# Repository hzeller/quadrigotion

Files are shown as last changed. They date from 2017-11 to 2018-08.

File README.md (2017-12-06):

Quadrigotion: Multiple Motor Drivers, one connector
============================================================

Often it is useful to have all the motor drivers needed for a machine
on a separate circuit board to be able to mount it to a heatsink or close
to the action. This is what this project is about.
The name **Quadrigotion** is a word amalgamated from 'Quadriga' (Four
horses powering a chariot) and 'Motion'.

Motivation for this project to have motor drivers easily replacable and
testable on my various 3D printers and CNC machines. Since I am also
[developing motion control software][BeagleG], I might have an unusual
high demand for this :)

The idea is to have a common connector type, described below, and various
implementations of that concept. The first implementation is using a TMC2660,
which is the 'big brother' of the more well-known TMC2100.

Other implementations are conceivable e.g. with Pololu modules, DRV8825, or
super high current and voltage drivers for heavy CNC machines.
Implementations can be super bare-bone and not use the SPI connection or
could be configured via SPI using a shift-register and digital potentiometers
if the chips can't be configured with SPI directly.
While the first Quadrigotion implementation happens to also have four motor
drivers, this could of course extend in the future.

The Connector
--------------

The digital input is provided with an IDC connector with 16 pins (2x8) or
20 pins (2x10).
It features a SPI bus to send configuration data and also read motor/driver
status (the actual protocol is of implementation-dependent, but they all can
share the same hardware interface).

| Desc | Pin | Pin | Desc
|---:|:---:|:---:|:---
| GND  | 1 | 2 | VCC (3.3V-5V)
| All Motors ~Enable | 3 | 4 | (not connected; reserved for fault-out)
| ~CS (SPI) | 5 | 6 | CLK (SPI)
| MISO (SPI) | 7 | 8 | MOSI (SPI)
| Step #1 | 9 |  10 | Dir #1
| Step #2 |  11 |  12 | Dir #2
| Step #3 |  13 |  14 | Dir #3
| Step #4 |  15 |  16 | Dir #4 -------- END IDC 16 variant
| Step #5 |  17 |  18 | Dir #5
| Step #6 |  19 |  20 | Dir #6 -------- END IDC 20 variant

It is easy to see that extending the driver count would just require a wider
IDC connector; the serial configuration interface can deal with any
number. A 16 pin IDC connector allows for 4 steppers, the next configuration
with 20 pins would allow for six drivers.

A single Enable-pin is provided that affects all drivers. This makes it easy
to wire up that signal directly e.g. for emergency buttons.
If more individual control of each driver is needed, this can be done via
the SPI connection.

The fast signals for each stepper, step and dir, are provided in
a parallel input with two lines per stepper.

A Quadrigotion connector has a single ChipSelect signal; multiple drivers
on each implementation have to share that bus, e.g. by internally being
organized as a shift register that latches when ~CS goes high again.

One pin (pin 4) is not connected yet, but it is reserved for fault detection
output (e.g stalling, overheating or over-current).

In an upcoming project, I'll build a breakout board to work with [BeagleG].

TMC2660 Implementation
----------------------

The first implementation is based on the TMC2660, a feature-rich motor driver
that can drive up to 4A (2.8A RMS). The 40mmx125mm PCB is a four layer board
which duals as heat conductor for cooling. Multiple M2.5 mounting holes allow
to firmly mount it to a heatsink and get even pressure to individual silicone
heatsink pads.
Power is provided via a 4-pin JST VH connector (3.96mm pitch),
circuit protected with an automotive ATC Mini 297 blade fuse.

You find the gerbers in the [fab/](./fab) directory. Board is also
[shared on OshPark]. Cave: since this is the very first version, no
testing has been done yet with a physical board.

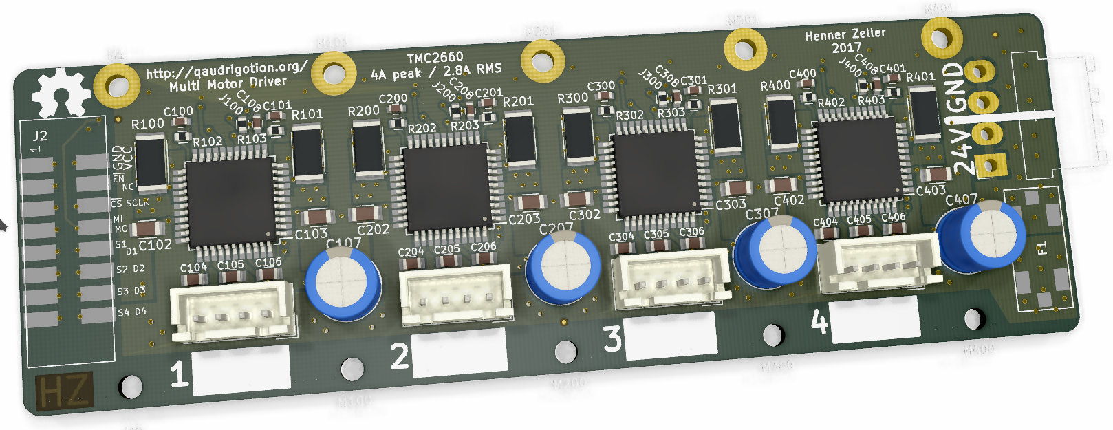
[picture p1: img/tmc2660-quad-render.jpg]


[BeagleG]: https://github.com/hzeller/beagleg
[shared on OshPark]: https://oshpark.com/shared_projects/M0SQCRdL

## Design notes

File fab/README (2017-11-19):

This directory contains gerber output files ready for fabbing.
These are generated from the KiCad boards.

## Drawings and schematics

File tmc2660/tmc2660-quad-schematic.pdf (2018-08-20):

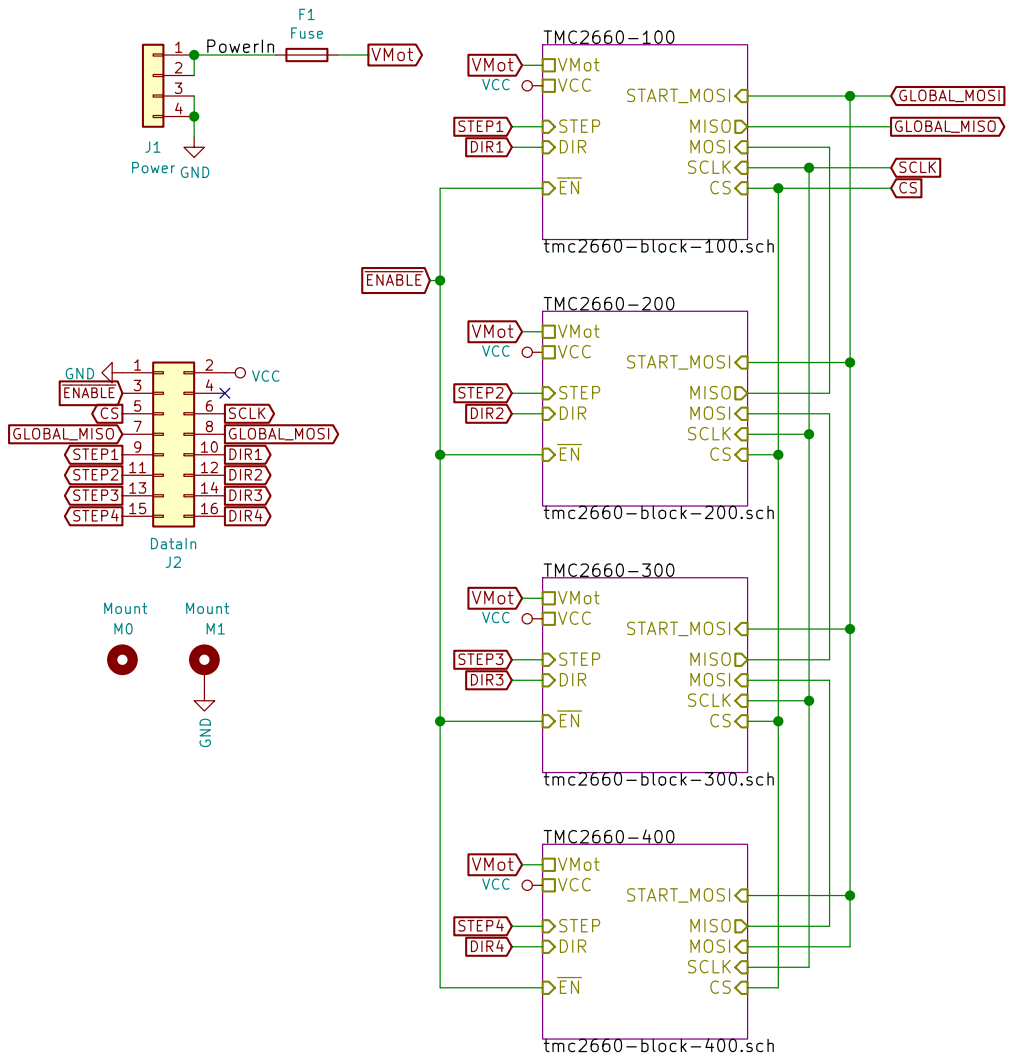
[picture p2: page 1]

File: tmc2660-quad.sch Sheet: / http://quadrigotion.org/

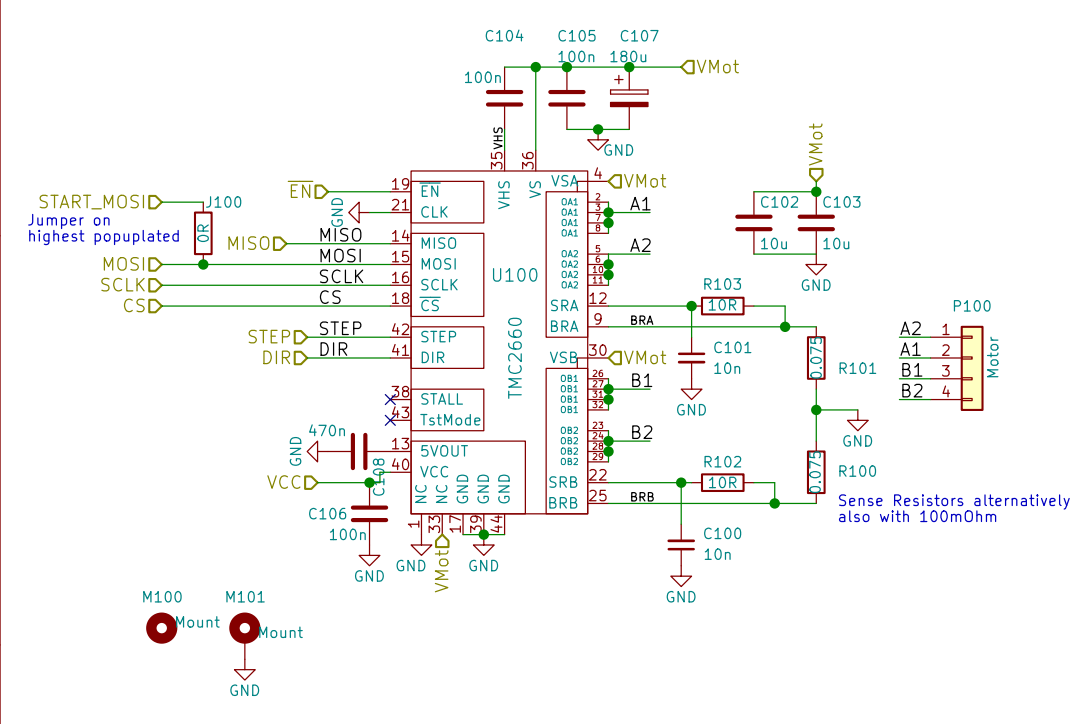
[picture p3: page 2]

Sense Resistors alternatively also with 100mOhm

File: tmc2660-block-100.sch Sheet: /TMC2660-100/ http://quadrigotion.org/

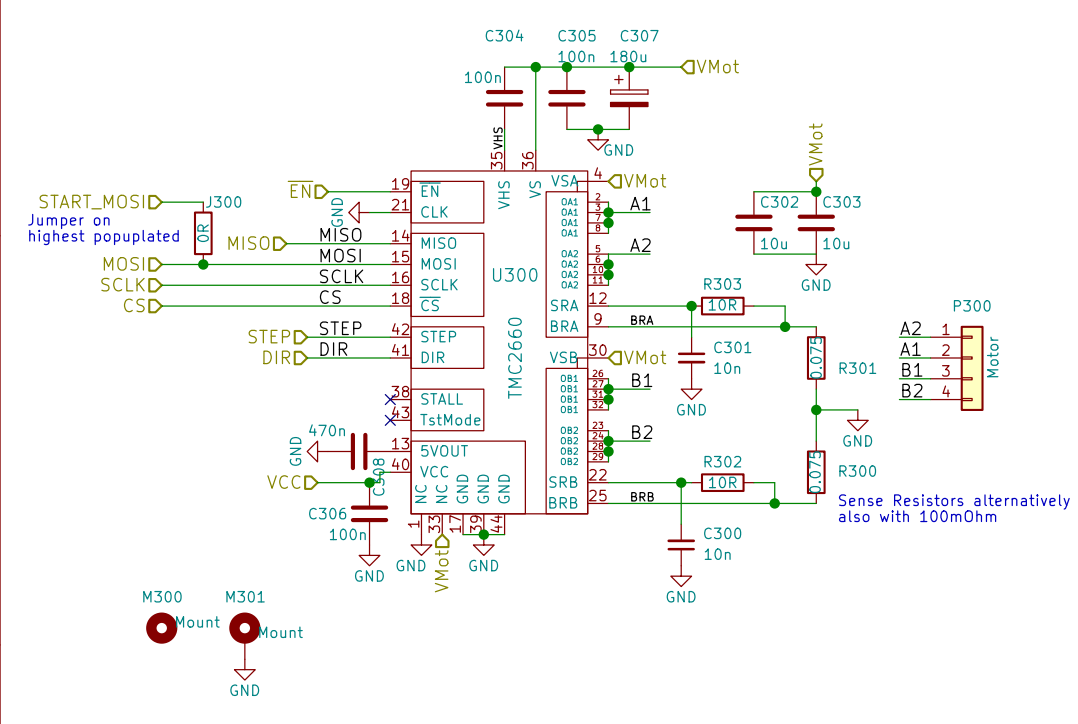
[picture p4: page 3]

Sense Resistors alternatively also with 100mOhm

File: tmc2660-block-300.sch Sheet: /TMC2660-300/ http://quadrigotion.org/

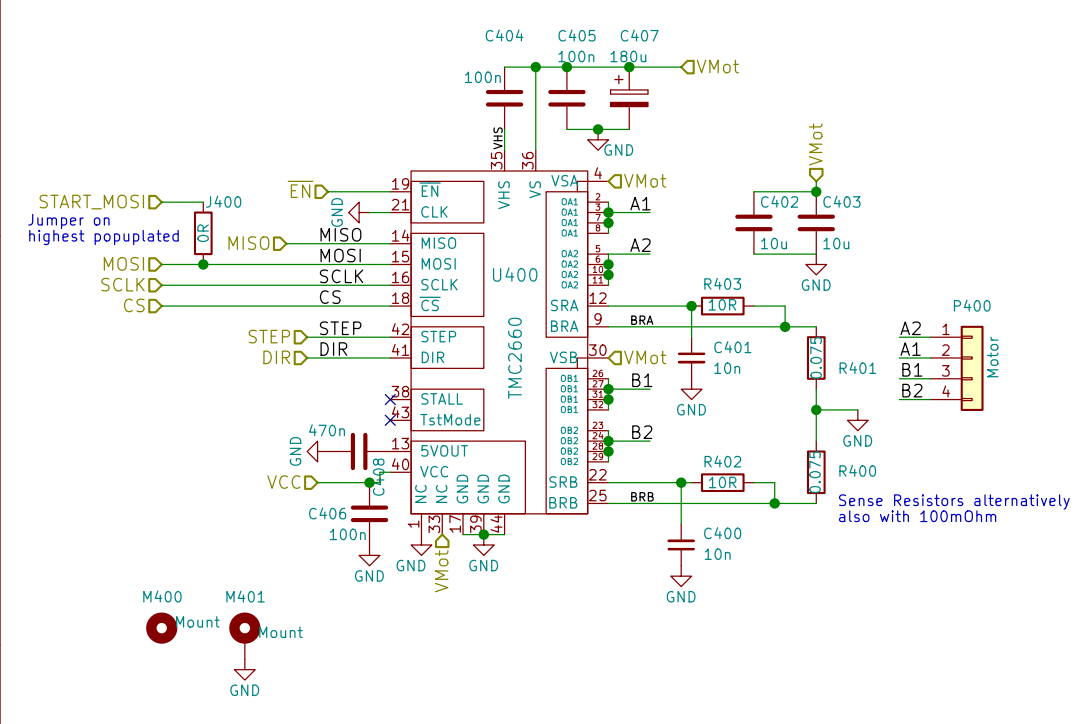
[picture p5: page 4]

Sense Resistors alternatively also with 100mOhm

File: tmc2660-block-400.sch Sheet: /TMC2660-400/ http://quadrigotion.org/

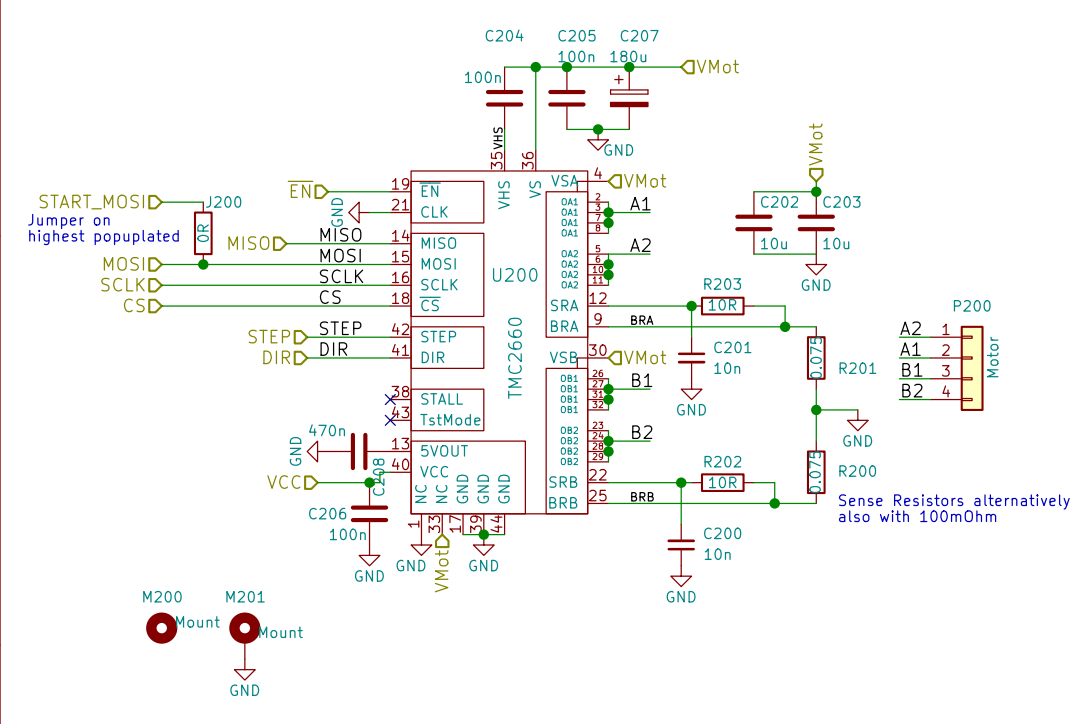
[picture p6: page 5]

Sense Resistors alternatively also with 100mOhm

File: tmc2660-block-200.sch Sheet: /TMC2660-200/ http://quadrigotion.org/

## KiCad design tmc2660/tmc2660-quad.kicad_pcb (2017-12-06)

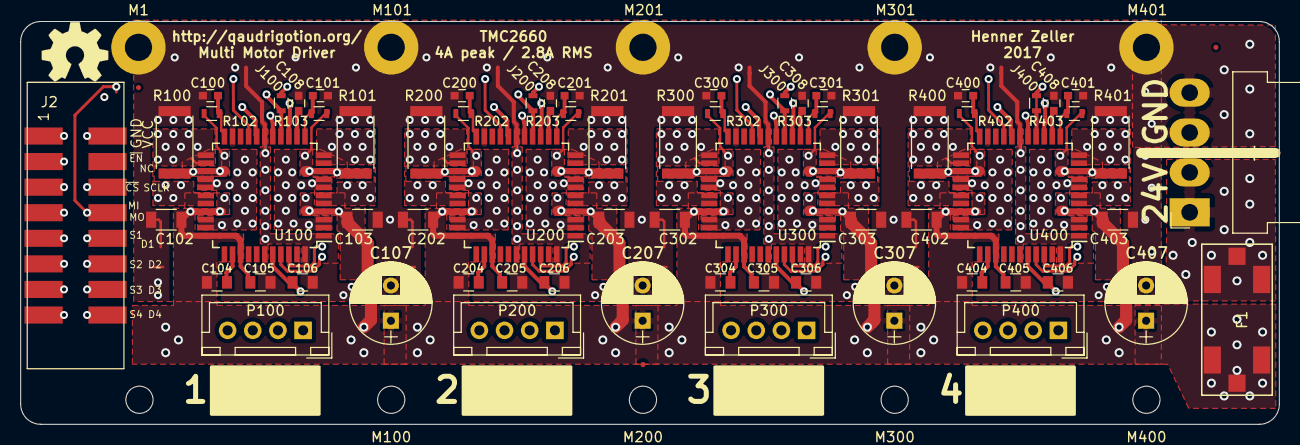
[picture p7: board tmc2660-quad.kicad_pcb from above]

Board: 4 copper layers, 125.0 x 40.0 mm, 77 parts (0 on the bottom side), 60 nets.

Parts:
C100, C101, C200, C201, C300, C301, C400, C401: 10n; C_0603
C102, C103, C202, C203, C302, C303, C402, C403: 10u; C_1206
C104, C105, C106, C204, C205, C206, C304, C305, C306, C404, C405, C406: 100n; C_0805
C107, C207, C307, C407: 180u; CP_Radial_D8.0mm_P3.50mm
C108, C208, C308, C408: 470n; C_0603
F1: Fuse; BladeFuse-Mini_Keystone-3586
J1: Power; JST_VH_B4PS-VH_2x4x3.96mm_Horizontal
J2: DataIn; IDC_Header_SMD_16pins
J100, J200, J300, J400: 0R; R_0603
M0, M100, M200, M300, M400: Mount; MountingHole_2.7mm_M2.5
M1, M101, M201, M301, M401: Mount; MountingHole_2.7mm_M2.5_Pad
P100, P200, P300, P400: Motor; JST_XH_B04B-XH-A_04x2.50mm_Straight
R100, R101, R200, R201, R300, R301, R400, R401: 0.075; R_2512
R102, R103, R202, R203, R302, R303, R402, R403: 10R; R_0603
U100, U200, U300, U400: TMC2660; LQFP-44_10x10mm_Pitch0.8mm

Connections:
/PowerIn: F1.2, J1.1, J1.2
/TMC2660-100/A1: P100.2, U100.2, U100.3, U100.7, U100.8
/TMC2660-100/A2: P100.1, U100.5, U100.6, U100.10, U100.11
/TMC2660-100/B1: P100.3, U100.26, U100.27, U100.31, U100.32
/TMC2660-100/B2: P100.4, U100.23, U100.24, U100.28, U100.29
/TMC2660-100/BRA: R101.1, R103.2, U100.9
/TMC2660-100/BRB: R100.1, R102.1, U100.25
/TMC2660-100/VHS: C104.2, U100.35
/TMC2660-200/A1: P200.2, U200.2, U200.3, U200.7, U200.8
/TMC2660-200/A2: P200.1, U200.5, U200.6, U200.10, U200.11
/TMC2660-200/B1: P200.3, U200.26, U200.27, U200.31, U200.32
/TMC2660-200/B2: P200.4, U200.23, U200.24, U200.28, U200.29
/TMC2660-200/BRA: R201.1, R203.2, U200.9
/TMC2660-200/BRB: R200.1, R202.1, U200.25
/TMC2660-200/MISO: J100.2, U100.15, U200.14
/TMC2660-200/VHS: C204.2, U200.35
/TMC2660-300/A1: P300.2, U300.2, U300.3, U300.7, U300.8
/TMC2660-300/A2: P300.1, U300.5, U300.6, U300.10, U300.11
/TMC2660-300/B1: P300.3, U300.26, U300.27, U300.31, U300.32
/TMC2660-300/B2: P300.4, U300.23, U300.24, U300.28, U300.29
/TMC2660-300/BRA: R301.1, R303.2, U300.9
/TMC2660-300/BRB: R300.1, R302.1, U300.25
/TMC2660-300/MISO: J200.2, U200.15, U300.14
/TMC2660-300/VHS: C304.2, U300.35
/TMC2660-400/A1: P400.2, U400.2, U400.3, U400.7, U400.8
/TMC2660-400/A2: P400.1, U400.5, U400.6, U400.10, U400.11
/TMC2660-400/B1: P400.3, U400.26, U400.27, U400.31, U400.32
/TMC2660-400/B2: P400.4, U400.23, U400.24, U400.28, U400.29
/TMC2660-400/BRA: R401.1, R403.2, U400.9
/TMC2660-400/BRB: R400.1, R402.1, U400.25
/TMC2660-400/MISO: J300.2, U300.15, U400.14
/TMC2660-400/VHS: C404.2, U400.35
CS: J2.5, U100.18, U200.18, U300.18, U400.18
DIR1: J2.10, U100.41
DIR2: J2.12, U200.41
DIR3: J2.14, U300.41
DIR4: J2.16, U400.41
GLOBAL_MISO: J2.7, U100.14
GLOBAL_MOSI: J2.8, J100.1, J200.1, J300.1, J400.1, J400.2, U400.15
GND: C100.1, C101.2, C102.2, C103.2, C105.2, C106.2, C107.2, C108.2, C200.1, C201.2, C202.2, C203.2, C205.2, C206.2, C207.2, C208.2, C300.1, C301.2, C302.2, C303.2, C305.2, C306.2, C307.2, C308.2, C400.1, C401.2, C402.2, C403.2, C405.2, C406.2, C407.2, C408.2, J1.3, J1.4, J2.1, M1.1, M101.1, M201.1, M301.1, M401.1, R100.2, R101.2, R200.2, R201.2, R300.2, R301.2, R400.2, R401.2, U100.1, U100.17, U100.21, U100.39, U100.44, U200.1, U200.17, U200.21, U200.39, U200.44, U300.1, U300.17, U300.21, U300.39, U300.44, U400.1, U400.17, U400.21, U400.39, U400.44
unnamed: C100.2, R102.2, U100.22
unnamed: C101.1, R103.1, U100.12
unnamed: C108.1, U100.13
unnamed: C200.2, R202.2, U200.22
unnamed: C201.1, R203.1, U200.12
unnamed: C208.1, U200.13
unnamed: C300.2, R302.2, U300.22
unnamed: C301.1, R303.1, U300.12
unnamed: C308.1, U300.13
unnamed: C400.2, R402.2, U400.22
unnamed: C401.1, R403.1, U400.12
unnamed: C408.1, U400.13
SCLK: J2.6, U100.16, U200.16, U300.16, U400.16
STEP1: J2.9, U100.42
STEP2: J2.11, U200.42
STEP3: J2.13, U300.42
STEP4: J2.15, U400.42
VCC: C106.1, C206.1, C306.1, C406.1, J2.2, U100.40, U200.40, U300.40, U400.40
VMot: C102.1, C103.1, C104.1, C105.1, C107.1, C202.1, C203.1, C204.1, C205.1, C207.1, C302.1, C303.1, C304.1, C305.1, C307.1, C402.1, C403.1, C404.1, C405.1, C407.1, F1.1, U100.4, U100.30, U100.33, U100.36, U200.4, U200.30, U200.33, U200.36, U300.4, U300.30, U300.33, U300.36, U400.4, U400.30, U400.33, U400.36
~ENABLE: J2.3, U100.19, U200.19, U300.19, U400.19

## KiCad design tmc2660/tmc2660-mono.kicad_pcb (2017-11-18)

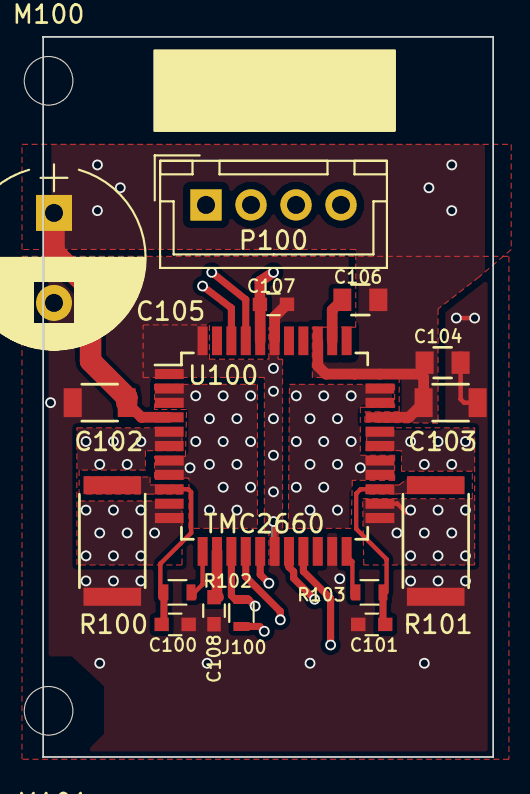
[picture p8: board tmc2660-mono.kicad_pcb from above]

Board: 4 copper layers, 25.0 x 40.0 mm, 18 parts (0 on the bottom side), 14 nets.

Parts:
C100, C101: 10n; C_0603
C102, C103: 10u; C_1206
C104, C106: 100n; C_0805
C105: 100u; CP_Radial_D10.0mm_P5.00mm
C107: 100n; C_0603
C108: 470n; C_0603
J100: 0R; R_0603
M100, M101: Mount; MountingHole_2.7mm_M2.5
P100: Motor; JST_XH_B04B-XH-A_04x2.50mm_Straight
R100, R101: 0.075; R_2512
R102, R103: 10R; R_0603
U100: TMC2660; LQFP-44_10x10mm_Pitch0.8mm

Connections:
/TMC2660-Block/A1: P100.2, U100.2, U100.3, U100.7, U100.8
/TMC2660-Block/A2: P100.1, U100.5, U100.6, U100.10, U100.11
/TMC2660-Block/B1: P100.3, U100.26, U100.27, U100.31, U100.32
/TMC2660-Block/B2: P100.4, U100.23, U100.24, U100.28, U100.29
/TMC2660-Block/BRA: C100.2, R100.1, R102.2, U100.9
/TMC2660-Block/BRB: C101.1, R101.1, R103.1, U100.25
/TMC2660-Block/MISO: J100.2, U100.14
GND: C100.1, C101.2, C102.2, C103.2, C104.2, C105.2, C107.2, C108.2, R100.2, R101.2, U100.1, U100.17, U100.21, U100.39, U100.44
unnamed: C106.2, U100.35
unnamed: C108.1, U100.13
unnamed: R102.1, U100.12
unnamed: R103.2, U100.22
VCC: C107.1, U100.40
VMot: C102.1, C103.1, C104.1, C105.1, C106.1, U100.4, U100.30, U100.33, U100.36

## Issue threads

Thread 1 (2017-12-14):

Affordabilty of PCBs

Duckle29, 2017-12-14:
I'm looking at getting a few of these made for sure, for my current printer, and was pricing it out.

At the current dimensions, 125 * 40mm I'm looking at 36 USD on easy EDA for 5 boards. That's 7.29 USD/board

If the board was instead 100 * 50mm (same area) you could panelize two of those together with v-grooves between them, which means you could get 10 boards for 32 USD, which would be  3.2 USD/board

This is because as long as you are within a 100x100mm panel, you fall into their cheap "this is what we have a price war on" price, but when you go over 100mm, you just get a "sq mm" price.

Duckle29, 2017-12-14:
I'll take a stab at fitting the design in that area in the weekend for sure :) I feel like moving the connectors at the ends down should do the trick.

hzeller, 2017-12-14:
Yeah, unfortunately, I couldn't squeeze it in 100mm, I tried :) Unfortunately, 4-layer boards really only start to be affordable with a little more quantity.

I have a couple of earlier version boards (version from 2017-11-19), that is mostly the same as the last version with only one minor issue that doesn't matter. If you are living in the US, I can send you one with domestic shipping (with components, it looks like [this](https://plus.google.com/u/0/+HennerZeller/posts/ZPCogGqCQMK). I have not tested it yet, hopefully this weekend will be time). So if you want one, send me your address via email.

Duckle29, 2017-12-14:
I'm in Denmark, but no need :) I kinda want to do the jiggling and give it a shot :P

I see that post you linked brought up a question I also have. Exact protocol. The datasheet isn't super clear on it. I was interested in how you got data out of them. I suppose just shifting in the appropriate query command to the appropriate chip, then keeping clocking until the message shifted its way through all of the chips?

hzeller, 2017-12-14:
I need to test that again; last time I played with it was a while back.
I think what happens is, while you shift in configuration bits, the current status bits come out on the other side, followed whatever is spilled over from the shift register.

So it should be possible to shift in 4x configuration data that then end up in the right chips and 4x status data has come out on the other side by then.

Duckle29, 2017-12-14:
Interesting

hzeller, 2017-12-14:
I'll update the readme once I played with it.

Duckle29, 2017-12-14:
6.3 Bus Architecture in the datasheet is what I needed to read. They work just like switch registers when chained, meaning that if you want to read from all of them, you can send 4 read commands, then clock in 160 pulses to shift that back to the master.

Duckle29, 2017-12-14:
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

From reading the datasheet. I think it's something like that. I'm not 100% sure if you need to pull CSN low again after sending the 4 commands, or if the interface will happily shift away with CSN high.

So the only thing I'm unsure of would be CSN.

Duckle29, 2017-12-15:
You can check out my work in my fork. I'm almost done with power, and now only have to get to data, but that's for another day.

Duckle29, 2017-12-15:
I think I'm done. I just need to move the graphics in. If you are interested. I'd love for you to check out the routing. I've cut a few pours, but I'm fairly certain everything should be able to handle 5A per driver.

I've also implemented the Stallguard pin, buy using 4 diodes common cathode, to a pulldown resistor. This effectively works like a 4 input or gate :)

hzeller, 2017-12-15:
Don't forget to push your changes, your github still shows yesterdays' state.

Duckle29, 2017-12-15:
Thanks for the reminder. Pushed :P

hzeller, 2017-12-15:
NIce. Some smallish things I noticed:

  - Pin 4 of your power connector is not connected to ground. Looks like a Junction went missing in the schematic.
  - The zones around the power connector pins are not with THT-Thermal. It might be hard to solder.
  - Like GND, I'd probably stitch a couple of inner layers to the PowerIn part as well; we have the copper, we should use it.
  - The diode array is inside the IDC connector courtyard. It might work, as they usually 'hover' a little, but if there is the space, probably keeping it outside is a good idea.
- there is a break of the copper pour on the inner layer 1 between the R300 resistor and Pin 17 of the corresponding TMC2660. Not a big deal too much (as the other layers take care of that) but we want to have the potential of GND not fluctuate too much as the shunt output is measured towards this ground.

Duckle29, 2017-12-15:
Thanks :) For high power pins, I prefer the inconvenience when soldering, to instead have a nice solid connection to the board, physically and electrically :)

As for stitching, how necessary is it, when the gnd input is through hole? IIRC I have gnd pour on all 4 layers from the power input :)

Duckle29, 2017-12-15:
Also fixed the pour around R300

Duckle29, 2017-12-22:
I might be getting a few of these made in Jan or Feb, I'll send you one if you want?

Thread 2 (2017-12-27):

Upgrading a Smoothie Board

KarlZeilhofer, 2017-12-27:
Hi,

have you thought about using your Trinamics board on upgrading a somoothie board ( http://smoothieware.org/smoothieboard )

They want to provide Trinamic drivers but with no schedule. So fitting your board to a smoothie board v1.1 could be an intermediate solution.

Greets,
Karl

hzeller, 2017-12-27:
Should be pretty straightforward if you ask me; if they provide an IDC connector like specified, it should be pretty simple to add. The step/dir is the same, but it requires some little initialization code for the SPI configuration. Having such connector would be great anyway so that we can separate the implementation of the motion control part and the stepmotor drivers that might be built and chosen for various power requirements.

Anyway, my first step is to make it work with [BeagleG](https://github.com/hzeller/beagleg) and get some experience to see if this is sufficient (I still need to provide a fault-out on pin 4), but then of course would like to see that other control boards also provide the simple connector to ultimately provide more choice in combinations people can use.

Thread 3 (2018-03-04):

Why the VMOT pours under the chip?

Duckle29, 2018-03-04:
Hey there. I was wondering why VMOT had rectangular pours under the chip

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

It's not present in the example layout from trinamic, and I can't seem to find any info on the pins being use for cooling.

hzeller, 2018-03-06:
Yes, this is meant as part of the cooling with the vias bolting together top and bottom transferring heat. More copper, even inner copper helps.
The cooling requirements are described in 14.3 in the TMC2660 datasheet and also shown a little in the 14.5 sample layout (though they don't do a good job there)

Duckle29, 2018-03-06:
Okay good to hear, and thanks for the pointer to the section that mentions it :)

Closed 2018-03-06.

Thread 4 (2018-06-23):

Step stick format?

boelle, 2018-06-23:
Do you have any plans to make a step stick format of the board?

of course only a single chip can fit on the board

just a thought, been using google to see if it has been done and your board is what comes close

rafaljot, 2018-07-03:
no way to place tmc2660 in step stick format. Maybe vertically.
Panucatt made"Bigfoot"
https://www.panucatt.com/azteeg_X5_GT_reprap_3d_printer_controller_p/ax5gt.htm

boelle, 2018-07-03:
bigfoot is not a stepper driver

all their stepper drivers are here: http://www.panucatt.com/category_s/1832.htm

sadly no 2660

snmcma, 2018-11-12:
Is there an error in the board on the j400 element? both pins are connected together

Closed 2019-03-19.

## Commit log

2017-11-12 Starting by preparing the tmc2660 breakout to be used in sequence.
    o Mostly preparing that the motor voltage carrying traces enter and leave
    at the same position right and left of the board.
    o No logical connection yet: Step/Dir and SPI bus will be routed in an
    inner layer.
    o (it is not clear yet if it will be simple to copy/paste a template
    board design easily; but we'll make it work)
    [tmc2660-quadrigotion.kicad_pcb, tmc2660-quadrigotion.sch]
2017-11-12 Use smaller connector. JST XH is sufficient for the currents at hand, no need for JST VH
    o Also: size adaption. The smaller connector allows to make the board a little
    narrower.
    o Add copper pour for VMOT.
    [tmc2660-quadrigotion.kicad_pcb, tmc2660-quadrigotion.sch]
2017-11-12 Prepare the inner layers.
    o Mostly one layer GND and VMOT.
    o Have copper fills for all the heatsinking regions to create a good
    heat-conductive connection top to bottom.
    o One layer leave mostly free for signals (except VMOT which is
    somewhat out of the way anyway and the heatsinking zones).
    o No signals routed yet (probably only going to happen once the
    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
    [tmc2660-quadrigotion.kicad_pcb]
2017-11-13 Fix mis-labelled pin in schematic symbol.
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2017-11-14 Wire up SPI in signal layer; prepare Step/Dir.
    [tmc2660-quad.kicad_pcb, tmc2660-quad.sch]
2017-11-14 Add mounting holes; trim sizes to 'round' values.
    o Size of board is 25mmx40mm
    o Distance M2.5 mounting holes: 35mm
    o Width needs to be a 'round' number so that replicated
    drivers have properly distanted mounting holes.
    [tmc2660-quad.kicad_pcb]
2017-11-14 Allow motor voltage around mounting hole in inner layers.
    Outer layers should not carry motor voltage near the mounting screw
    in case the soldermask gets damaged. Inner layers are ok and provide
    a an additional nice low-impedance path.
    [tmc2660-quad.kicad_pcb]
2017-11-14 Move some designator markings; Make screws frame chip.
    Also, add a filled silkscreen square for manual sharpie markings.
    ... alas, the gerber export for that seems to not work yet in the
    KiCAD version I am using.
    [tmc2660-quad.kicad_pcb]
2017-11-14 Rename the building block for the eventual quad tmc2660-mono.
    [tmc2660-mono.kicad_pcb, tmc2660-mono.sch]
2017-11-14 Adapt some vias around the SPI connect to fix a gap in the TopCu copper pour.
    [tmc2660-mono.kicad_pcb]
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2017-11-16 More sensible annotations, starting in the 100 range.
    [tmc2660-block.sch, tmc2660-mono.kicad_pcb]
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2017-11-18 Move template to separate dir. Adapt KiCAD 5.0 symbol lib.
    [tmc2660-block.sch, tmc2660-mono.kicad_pcb, tmc2660-mono.sch]
2017-11-18 Basic Schematic with cloned hierarchical sub-schematics for each block.
    [tmc2660-block-100.sch, tmc2660-block-200.sch, tmc2660-block-300.sch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]
2017-11-18 Consistently name first block TMC2660-100 in schematic and pcb.
    [tmc2660-block.sch, tmc2660-mono.kicad_pcb, tmc2660-mono.sch]
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2017-11-18 Start with MOSI on the right; turn around board.
    - Turn template board upside down, so that the IDC data connector
    can be on the left, and the motor outputs are marked 1..4 seen
    from there.
    - Instead of the last chip returning its output, we have it
    receive the MOSI. That way, the leftmost chip is naturally
    number 1 in the sequence of the shift register.
    [tmc2660-block.sch, tmc2660-mono.kicad_pcb, tmc2660-mono.sch]
2017-11-19 Wire up quad according to new MISO/MOSI sequence.
    - Also, add basic STEP/DIR and a capacitor.
    [tmc2660-block-100.sch, tmc2660-block-200.sch, tmc2660-block-300.sch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]
2017-11-19 Initial version of PCB with cloned template components.
    [tmc2660-block-100.sch, tmc2660-block-200.sch, tmc2660-block-300.sch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]
2017-11-19 Add leftmost screw holes; Move IDC connector down.
    [tmc2660-block-300.sch, tmc2660-quad.kicad_pcb, tmc2660-quad.sch]
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2017-11-19 Fix Makefile to refer to current file.
2017-11-19 Fix gap in copper pour.
    [tmc2660-mono.kicad_pcb]
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2017-11-19 Add labels.
    o White label areas under connectors for the user to write
    the logical axis with sharpie.
    o gitversion, github address etc.
    [tmc2660-quad.kicad_pcb]
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2017-11-19 Move bottom silkscreen a little ouf of the way of vias.
    o Also: larger vias in the general power input area.
    [tmc2660-quad.kicad_pcb]
2017-11-20 Fix some traces that unnecessarily have been pushed through copper fills.
    [tmc2660-quad.kicad_pcb]
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2017-11-22 Replace polygons with zones that are less broken objects.
    [tmc2660-quad.kicad_pcb]
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2017-11-24 More DFM: choose more common physical capacitor sizes.
    o Capacitors in the 100-150uF and 35-50V range are typically 8mm dia.
    o Choose all 100nF same size. Even for 50V, there are 0603 available.
    o Properly connect the 10nF smoothing capacitor for shunt feedback
    voltage (was connected to GND on the wrong side).
    [tmc2660-block.sch, tmc2660-mono.kicad_pcb]
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2017-11-26 Update tmc2660-quad with new template.
    o Start out with a tmc2660-quad-baseline that is filled
    in with zones and tracks from the template.
    o The separation from baseline and template allows faster
    updates later.
    [tmc2660-block-100.sch, tmc2660-block-200.sch, tmc2660-block-300.sch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]
2017-11-26 Remove comment zone from template.
    o We're not requiring anymore to have a comment zone around the
    relevant parts, as we now separate template from board to be
    edited.
    [tmc2660-mono.kicad_pcb]
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2017-11-26 Add front silkscreen. Re-add center fiducial.
    o Front silkscreen and center fiducial got lost in the previous
    steps.
    o Re-add in the baseline file and re-generate the final file.
    [tmc2660-quad-baseline.kicad_pcb, tmc2660-quad.kicad_pcb]
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2017-11-27 GND plane around Step/Dir. Tighter routing of Step/Dir.
    [tmc2660-quad-baseline.kicad_pcb]
2017-11-27 Better choice of common component size; GND mounting hole.
    o 50V ceramic capacitors are easier and cheaper to get in 0805
    o Mounting holes near GND should be grounded to have a known
    potential for the heatsink.
    [tmc2660-block.sch, tmc2660-mono.kicad_pcb, tmc2660-mono.sch]
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2017-11-30 Add signal description also on front silk-screen.
    o In template: move a designator out of the way to not collide with that
    description.
    [tmc2660-mono.kicad_pcb, tmc2660-quad-baseline.kicad_pcb]
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2017-12-05 Improve readability designators.
    o Larger font if possible.
    o Avoid printing over vias if possible.
    [tmc2660-mono.kicad_pcb]
2017-12-06 Move VMOT 100nF input stabilisator for VHS voltage regulator close to pin.
    o Re-number the 100nF capacitors that they show up in an increasing numbers
    o Use opportunity to move silkscreen of 10uF capacitors out of via's harms way.
    [tmc2660-block-100.sch, tmc2660-block-200.sch, tmc2660-block-300.sch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]
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2017-12-16 Fix data direction of some direction labels :)
    [tmc2660-quad.sch]
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
